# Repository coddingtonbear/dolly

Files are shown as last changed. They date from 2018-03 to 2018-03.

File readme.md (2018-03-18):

# Dolly

Dolly is a GRBL controller board that my existing "Woodpecker" GRBL controller board
will make for me.  It includes a few features that my CNC machine's stock
board did not offer including:

* JST-XH connectors for spindle, probe, and end stop connections.
* Bluetooth connectivity via an on-board HC-05 module.
* On-Board ICSP header to allow for reflashing without using USB Bootloader.

## Errata

* Nothing so far!

## Future Ideas

* Consider using STM32 or ESP32 as main CPU.  Currently, GRBL is designed to run on only the ATMEGA328p chip, and although ports to STM32F103 and ATMEGA2560 do exist, they're handled as one-offs by individuals interested in those ports.  In the future, there is expected to be an abstraction layer in GRBL's core allowing for simpler use of non-328p chips.  Once that's a possibility, using a more modern chip would become a more compelling option.
* Maybe use a buck regulator for stepping-down the 24v input to 3.3v instead of a (series of) linear regulators.  I didn't use a buck regulator in this design because one of the major reasons I'm building this is to hopefully get away from some EMI and heat management problems I have with my current board.  Alternatively, step down directly to 3.3v; the only reason I used a series of regulators here is that I don't have any 3.3v regulators on-hand that have input voltage ceilings as high as 24v.

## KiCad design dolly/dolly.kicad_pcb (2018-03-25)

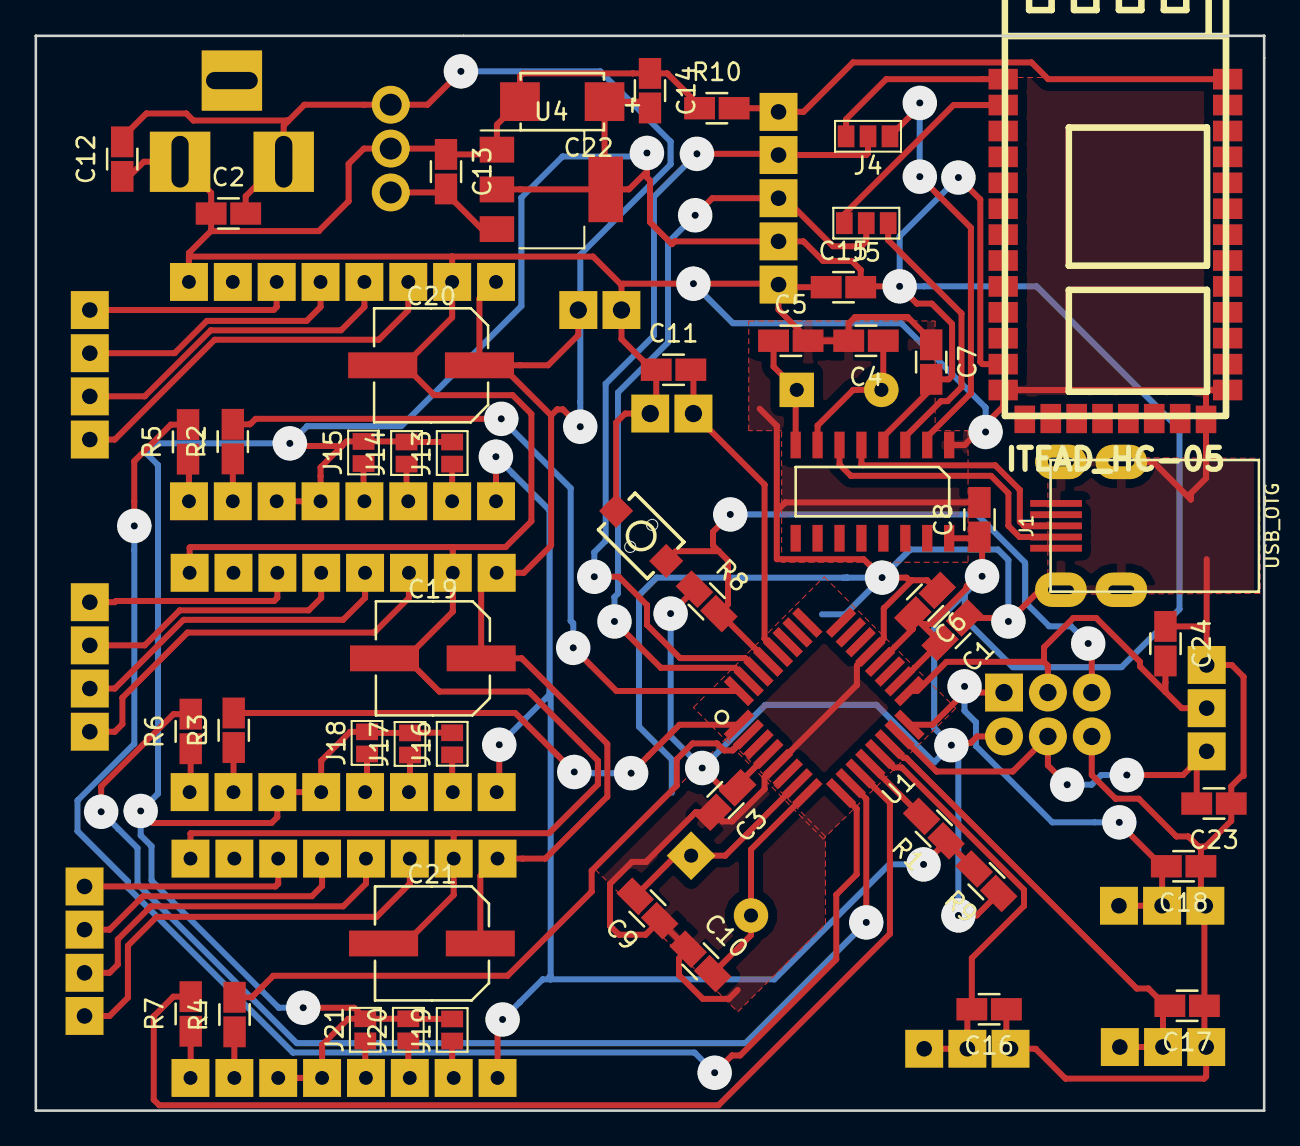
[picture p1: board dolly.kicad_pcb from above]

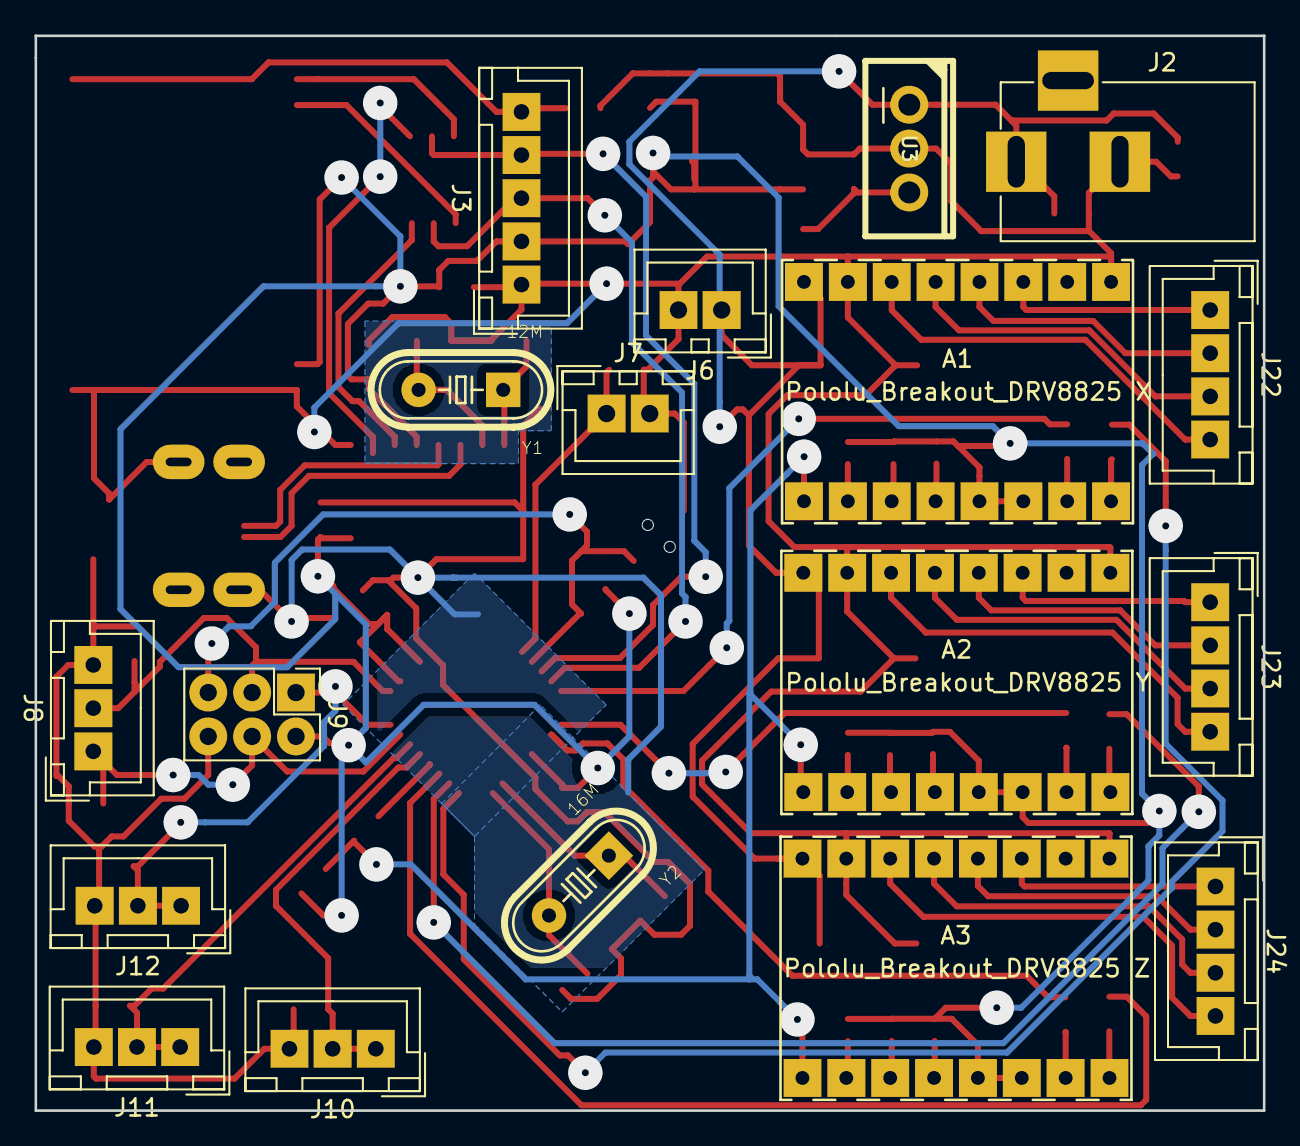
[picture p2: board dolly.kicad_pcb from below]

Board: 2 copper layers, 71.1 x 62.2 mm, 69 parts (18 on the bottom side), 59 nets.

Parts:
A1: Pololu_Breakout_DRV8825 X; Pololu_Stepper_Breakout
A2: Pololu_Breakout_DRV8825 Y; Pololu_Stepper_Breakout
A3: Pololu_Breakout_DRV8825 Z; Pololu_Stepper_Breakout
C1, C2, C3, C6, C7, C8, C11, C14, C15, C16, C17, C18, C23, C24: 0.1u; 0805_Milling
C4, C5, C9, C10: 22p; 0805_Milling
C12, C13: 0.33u; 0805_Milling
C19, C20, C21: 100u; CAP-SMD-SIZE-D
C22: 220u; CAPACITOR_TANTALUM_C
J1: USB_OTG; UJ2-MIBH-4-SMT
J2: Barrel_Jack; BARREL_JACK
J3: UART; JST_XH_B05B-XH-A_05x2.50mm_Straight_LargePads
J4: RX; GS3
J5: TX; GS3
J6: 24V_Out; JST_XH_B02B-XH-A_02x2.50mm_Straight_LargePads
J7: Probe; JST_XH_B02B-XH-A_02x2.50mm_Straight_LargePads
J8: Spindle; JST_XH_B03B-XH-A_03x2.50mm_Straight_LargePads
J9: ICSP; Pin_Header_Straight_2x03_Pitch2.54mm
J10: X_End; JST_XH_B03B-XH-A_03x2.50mm_Straight_LargePads
J11: Y_End; JST_XH_B03B-XH-A_03x2.50mm_Straight_LargePads
J12: Z_End; JST_XH_B03B-XH-A_03x2.50mm_Straight_LargePads
J13, J14, J15, J16, J17, J18, J19, J20, J21: GS2
J22: X_Stepper; JST_XH_B04B-XH-A_04x2.50mm_Straight_LargePads
J23: Y_Stepper; JST_XH_B04B-XH-A_04x2.50mm_Straight_LargePads
J24: Z_Stepper; JST_XH_B04B-XH-A_04x2.50mm_Straight_LargePads
R1, R2, R3, R4, R5, R6, R7: 100; 0805_Milling
R8, R9, R10: 10k; 0805_Milling
SW1: SW_SPST; SW_PUSHBUTTON_TINY_2PIN
U1: ATMEGA328PB-AU; TQFP32_ATMEGA328P
U2: CH340G; SOIC-16
U3: L7805; TO-220
U4: AP1117-15; SOT-223-3Lead_TabPin2
U5: ITEAD_HC-05
Y1: 12M; XTAL_HC-49US-16.000MHZ
Y2: 16M; XTAL_HC-49US-16.000MHZ

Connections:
+3V3: A1.13, A1.14, A2.13, A2.14, A3.13, A3.14, C1.2, C3.1, C6.2, C7.2, C8.1, C14.2, C15.2, C22.1, J3.2, J9.2, J13.2, J14.2, J15.2, J16.2, J17.2, J18.2, J19.2, J20.2, J21.2, R8.1, R9.1, U1.4, U1.18, U1.20, U2.4, U2.16, U4.2, U5.12
+24V: A1.8, A2.8, A3.8, C2.2, C12.2, C19.1, C20.1, C21.1, J2.1, J6.1, U3.1
BT_IN: J5.1, U5.2
BT_KEY: J3.5, R10.2, U5.34
BT_OUT: J4.1, U5.1
GND: A1.1, A1.7, A2.1, A2.7, A3.1, A3.7, C1.1, C2.1, C3.2, C4.2, C5.2, C6.1, C7.1, C8.2, C9.1, C10.1, C11.1, C12.1, C13.1, C14.1, C15.1, C16.1, C17.1, C18.1, C19.2, C20.2, C21.2, C22.2, C23.1, C24.1, J1.5, J1.6, J2.2, J3.1, J6.2, J7.2, J8.3, J9.6, J10.3, J11.3, J12.3, R10.1, SW1.2, U1.5, U1.21, U2.1, U3.2, U4.1, U5.13, U5.21, U5.22
MISO: C18.2, J9.1, J12.1, J12.2, U1.16
MOSI: C23.2, J8.1, J9.4, U1.15
unnamed: A1.3, J22.1
unnamed: A1.4, J22.2
unnamed: A1.5, J22.3
unnamed: A1.6, J22.4
unnamed: A1.10, J13.1
unnamed: A1.11, J14.1
unnamed: A1.12, J15.1
unnamed: A2.3, J23.1
unnamed: A2.4, J23.2
unnamed: A2.5, J23.3
unnamed: A2.6, J23.4
unnamed: A2.10, J16.1
unnamed: A2.11, J17.1
unnamed: A2.12, J18.1
unnamed: A3.3, J24.1
unnamed: A3.4, J24.2
unnamed: A3.5, J24.3
unnamed: A3.6, J24.4
unnamed: A3.10, J19.1
unnamed: A3.11, J20.1
unnamed: A3.12, J21.1
unnamed: C4.1, U2.7, Y1.2
unnamed: C5.1, U2.8, Y1.1
unnamed: C9.2, U1.7, Y2.1
unnamed: C10.2, U1.8, Y2.2
unnamed: C13.2, U3.3, U4.3
unnamed: J1.2, U2.6
unnamed: J1.3, U2.5
unnamed: R1.2, U1.12
unnamed: R2.2, U1.32
unnamed: R3.2, U1.1
unnamed: R4.2, U1.2
unnamed: R5.2, U1.9
unnamed: R6.2, U1.10
unnamed: R7.2, U1.11
PROBE: C11.2, J7.1, U1.28
RST: J9.5, R8.2, SW1.1, U1.29
RX: J3.4, J4.2, U1.30
SCK: C24.2, J8.2, J9.3, U1.17
TX: J3.3, J5.2, U1.31
USB_IN: J5.3, U2.3
USB_OUT: J4.3, U2.2
XDIR: A1.16, R5.1
XEND: C16.2, J10.1, J10.2, U1.13
XSTEP: A1.15, R2.1
YDIR: A2.16, R6.1
YEND: C17.2, J11.1, J11.2, U1.14
YSTEP: A2.15, R3.1
ZDIR: A3.16, R7.1
ZSTEP: A3.15, R4.1
~ENABLE_STEPPER: A1.9, A2.9, A3.9, R1.1, R9.2

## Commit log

2018-03-18 And so it begins...
    [dolly.kicad_pcb, dolly.sch]
2018-03-25 Adding optional 0.1uF capacitors between spindle direction/pwm pins and gnd.
    [dolly.kicad_pcb, dolly.sch]
